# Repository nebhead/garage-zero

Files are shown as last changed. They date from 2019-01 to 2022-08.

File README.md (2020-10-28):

# Garage-Zero

## Raspberry Pi Zero based Garage Door Control & Status

***Note:*** *This project is continuously evolving, and thus this readme will likely be improved over time, as I find the inspiration to make adjustments.  That being said, I'm sure there will be many errors that I have overlooked or sections that I haven't updated.*

This project was inspired by Chris Driscoll's "Idiot's Guide to a Raspberry Pi Garage Door Opener" (http://www.driscocity.com/idiots-guide-to-a-raspberry-pi-garage-door-opener/).  I've replicated Chris' hardware setup almost exactly, save for the Raspberry Pi Zero (instead of the Raspberry Pi Model B).  

Instead of using the WebIO libraries that Chris uses, I decided to implement things a bit differently, providing a dynamic webUI with bootstrap and Flask.  

Initially this project used Flask's native WSGI services without Gunicorn or nginx as a proxy.  However, I noticed that after some time, the app would become unresponsive.  After a little research, it appears that Flask's built in web server is for testing purposes only and shouldn't really be used in production.  With that said, I'm using Gunicorn and nginx to proxy web requests.  This is simple enough to configure and setup, however I had to redesign the application without the threading libraries, due to conflicts with Gunicorn.  Instead, I am using two processes running concurrently (control.py and app.py).  Control handles all of the RasPi GPIO interfaces, while App handles the web routes.  They communicate through a .json file that is human readable for simplicity.  

## Screenshots

The interface / webui is broken out into three main pages. The first is the dashboard view where you can check the current status of the garage door (whether it is open or closed), see the event history (button presses, opened/closed, notifications, reboots, etc.), and of course a large button to open/close the door (which also indicates green if closed, red if open).

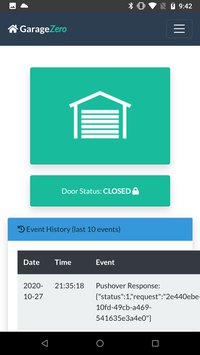
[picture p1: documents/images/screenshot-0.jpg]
Dashboard


Pressing the hamburger icon in the upper right of the interface, allows you to go to the history page, which gives you the detailed history of the last month of events.  

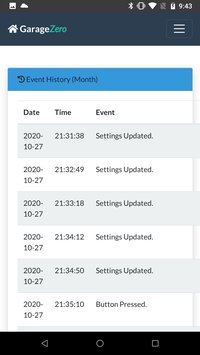
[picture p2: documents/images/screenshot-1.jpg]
History


Pressing the hamburger icon in the upper right of the interface, allows you to also access to the administration screen. This interface allows you to configure the notification settings (i.e. e-mail, IFTTT notifications, and Pushover notifications).

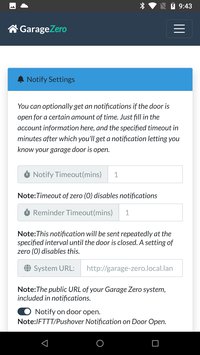
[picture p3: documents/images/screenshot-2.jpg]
Admin & Settings


Scrolling down gives you the ability to select from a few different themes including a 'dark mode' for those times when you don't want to blind yourself at night.  Then more system information following the theme settings.  

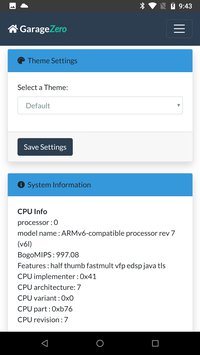
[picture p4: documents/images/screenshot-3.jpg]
Admin 2


Scrolling down further gives you the option to reboot the system or shutdown the system.  

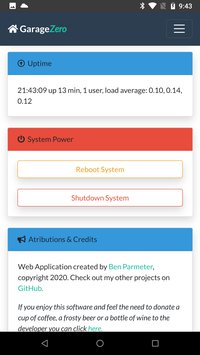
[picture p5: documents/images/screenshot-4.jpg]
Admin 3


## Hardware Configuration

### The Parts List
The parts list and setup of this was heavily borrowed from the following guide here: [http://www.driscocity.com/idiots-guide-to-a-raspberry-pi-garage-door-opener/](http://www.driscocity.com/idiots-guide-to-a-raspberry-pi-garage-door-opener/)

* **Raspberry Pi Zero W** - Technically any Raspberry Pi with wireless capability will do fine, but for this application a Raspberry Pi Zero W works really well.  
* **Case for Raspberry Pi** *(optional)* - It's a good idea to have a case for the Pi and other electronics to shield it from environmental abuse.  I personally decided to develop a 3D printed case and have shared the STL files for you if you want to duplicate my setup. [Link to case files.](documents/case) For reference, I used an Creality Ender 3 to print the case, with 0.12 layer height.  I'm reasonably happy with the finished product, but your mileage may vary.  
* **2-Channel Relay** - I use both channels for one single door to prevent any spurious door open signals from being sent during reboot/shutdowns. [Amazon Link](https://www.amazon.com/dp/B0057OC6D8/ref=cm_sw_em_r_mt_dp_U_jtppCb3FQ787B)
* **Magnetic Switch** (This is only necessary if you want to be able to determine if the door is open or closed) [Amazon Link](https://www.amazon.com/dp/B0009SUF08/ref=cm_sw_em_r_mt_dp_U_htppCbJ7B52KG)
* **Wire** for the magnetic switch and connecting the Raspberry Pi to your garage door opener (I used extra CAT6 cable I had laying around, any 2-conductor cable ~20-24 gauge should be fine)
* **Micro SD Card** - Greater than 4GB is probably good.  
* **MicroUSB Power Adapter** - At least 1 amp current recommended.  Make sure you have a place to plug this in near your garage door opener
* **10k Ohm resistor** - Used for the resistor divider circuit on the magnetic switch. Prevents the switch input from floating and causing spurious inputs.
* **1k Ohm resistor** - Used for the resistor divider circuit on the magnetic switch. Prevents the switch input from floating and causing spurious inputs.

### The Schematic

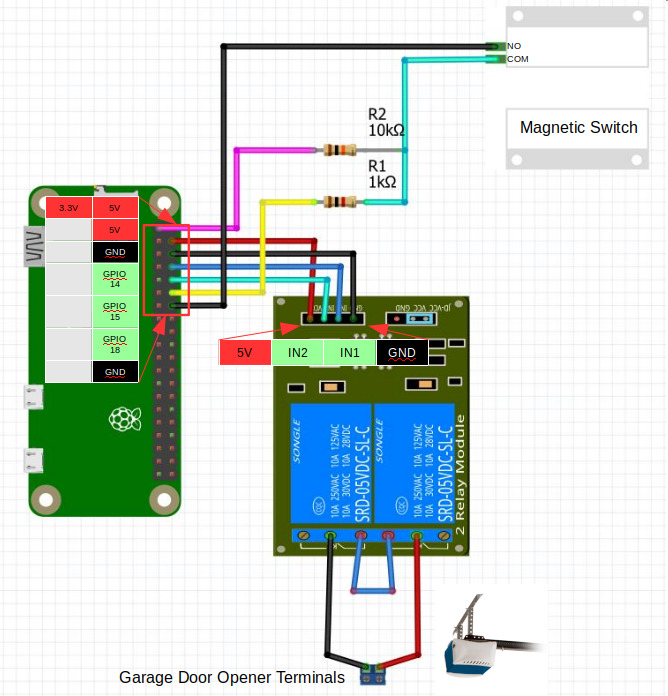
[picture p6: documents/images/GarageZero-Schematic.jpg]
Schematic


#### GPIO Mapping
The following GPIOs are mapped for this project:
* **GPIO15** - Output Relay Control (Open / Close Garage Door)
* **GPIO14** - Output Relay Control Gate (Prevents spurious open/close events during power-on, shutdown and reboot cycles) **IMPORTANT:** This relay should have a wire connected to the Normally Closed (NC) side of the relay. Otherwise, it will not function properly, preventing all button presses.
* **GPIO18** - Input for Magnetic Switch (Current State of Garage Door)

**Note:**  *Optional design change.*  Per user [hmoffatt](https://github.com/hmoffatt), there may not be a need for the 1k pull-down resistor.  It is probably OK to have the switch ground the input. Secondly there are fixed pull-up resistors of 1.8k on GPIOs 2 and 3 of the Raspberry PI. So you can just connect the switch directly to +3.3V and GPIO 2 or 3 without adding any extra resistors. If you make this design change, make sure you change the GPIO definition in the code from GPIO18 to GPIO2.  

**Note:** If you want to change which GPIOs you would like to use, please modify the control.py constants to what you want to use. Edit the following lines(*in control.py*):

```
    # GPIO Definitions
    relay_pin = 15			# GPIO 15, Pin 10 (RasPi Header)
    relay_gate_pin = 14		# GPIO 14, Pin 08 (RasPi Header)
    switch_pin = 18			# GPIO 18, Pin 12 (RasPi Header)
```

Truth Table for visualizing the output:

| IN1 | IN2 | Relay1 | Relay2 | Button Output |
|:---:|:---:|:---:|:---:|:---:|
|  0  |  0  | C | O | Not Pressed |
|  0  |  1  | C | C | Pressed |
|  1  |  0  | O | O | Not Pressed |
|  1  |  1  | O | C | Not Pressed |

*C=Closed/Connected*

*O=Open/Not Connected*

### Photos of the Hardware

A picture is worth a 1000 words.  With that, here is a bunch of pictures (with some words).  

Here is a picture of the Raspberry Pi Zero and the 2-channel relay module in the 3D-printed case.  Note that only the pins being used for GPIOs, GND, & Power on the header have been populated.  
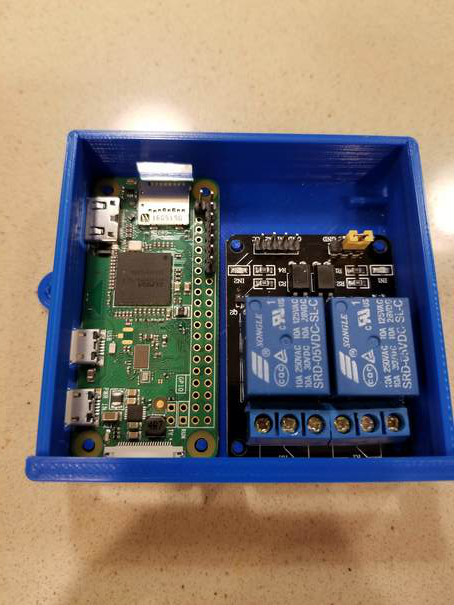
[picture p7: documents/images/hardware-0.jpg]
Case and Boards


I built this little daughter board to interface the Raspberry Pi with the 2-Channel relay board, as well as break-out wires for the magnetic switch/sensor.  The nice thing about this board is that it has headers that plug directly into the boards very easily (pictured here).
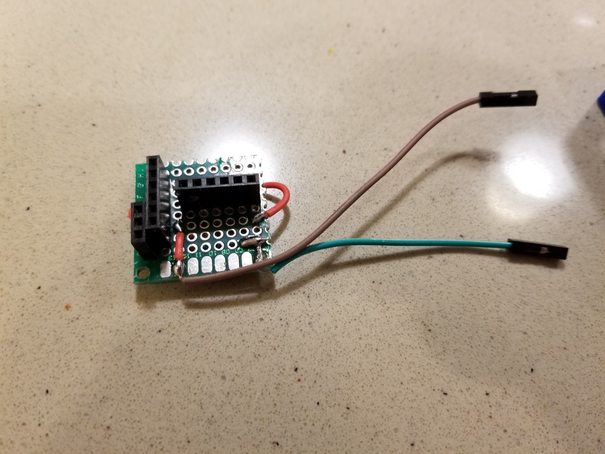
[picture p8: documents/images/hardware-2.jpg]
Daughter Board (Bottom)


This is picture of the top of the daughter board (and the case/rpi/relay), which has the wire routing, and the two resistors (for the voltage divider).  
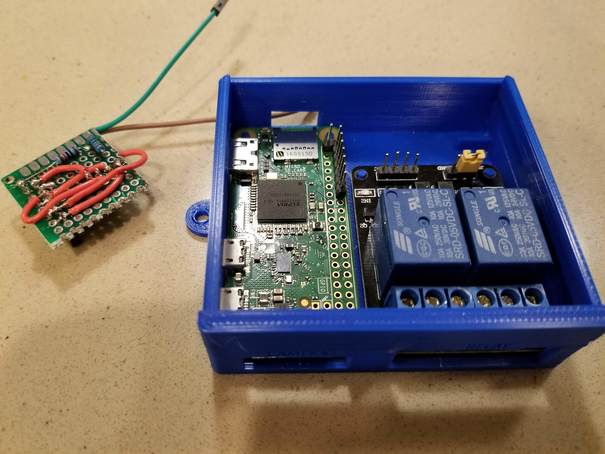
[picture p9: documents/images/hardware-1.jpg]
Daughter Board (Top), Case, RPi, Relay


Picture of the daughter board actually plugged into the raspberry pi and relay inside the case.  This gives you a picture of the scale.  
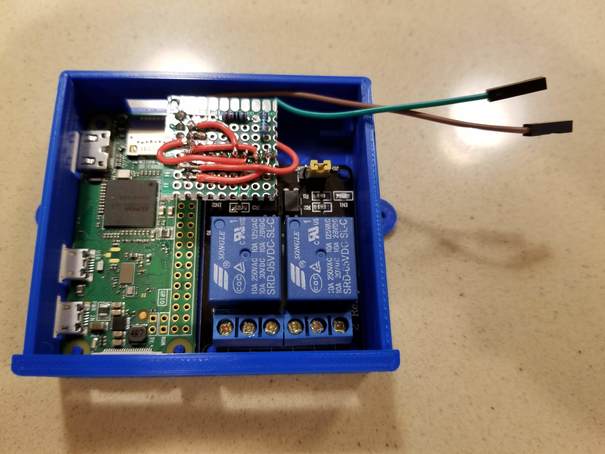
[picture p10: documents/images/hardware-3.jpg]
Daughter Board (Top) installed, Case, RPi, Relay


This is an attempt at showing the daughter board installed in both the raspberry pi and the relay.   
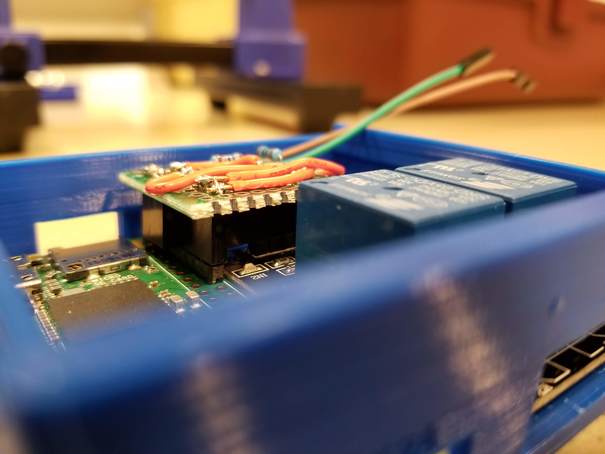
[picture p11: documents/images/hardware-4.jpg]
Daughter Board installed, side view


The female pin connectors are hot-glued into the space in the corner of the case so that the magnetic sensor can be easily connected via male jumper pins.  Note that the rest of the boards have been hot-glued into place.  
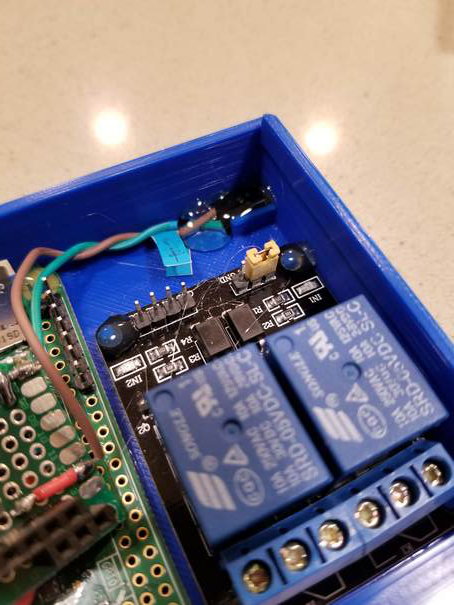
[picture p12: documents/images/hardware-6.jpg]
Hot Glue for the win


The assembled kit all together in the case, with lid.  Note that the screws are still accessible from the top.  
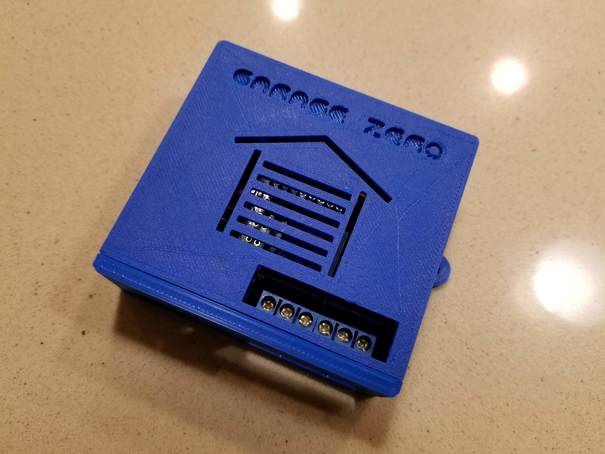
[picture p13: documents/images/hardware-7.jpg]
Case assembled


Case mounted to the beam directly above the garage door opener using two screws on either side of the case.  
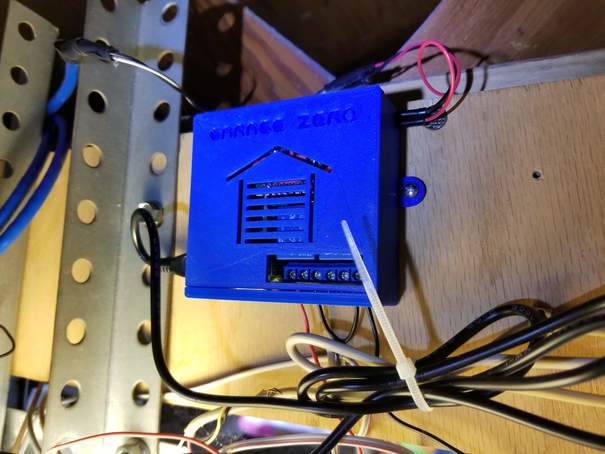
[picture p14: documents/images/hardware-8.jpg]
Installed above garage door opener


Another view of the installed case, with power cord. plugged in.
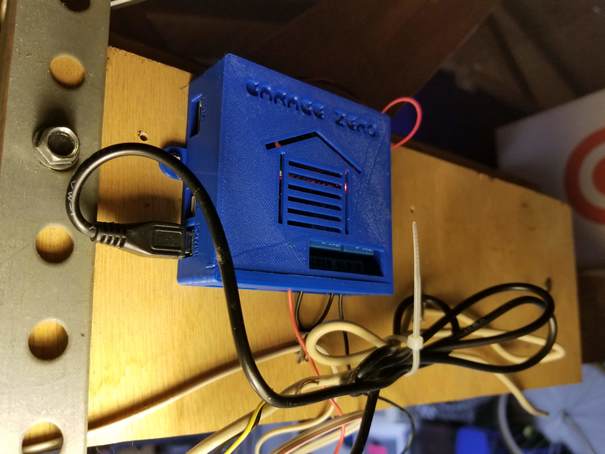
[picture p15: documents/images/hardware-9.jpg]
Installed view 2


Another view of the installed case, with the garage door opener for scale.
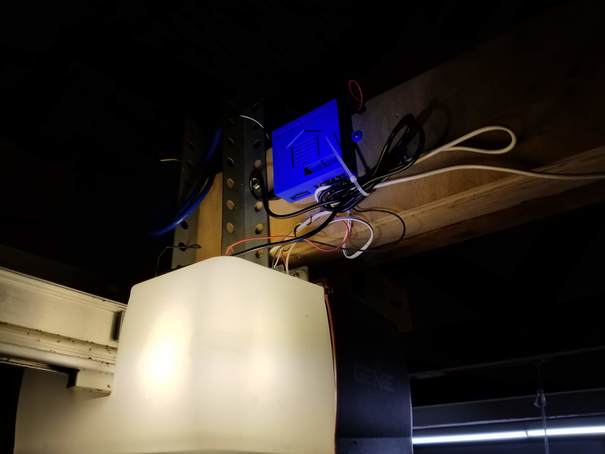
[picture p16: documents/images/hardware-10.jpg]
Installed view 3 zoomed out


Connections to the garage door opener terminals from the relay in the case.
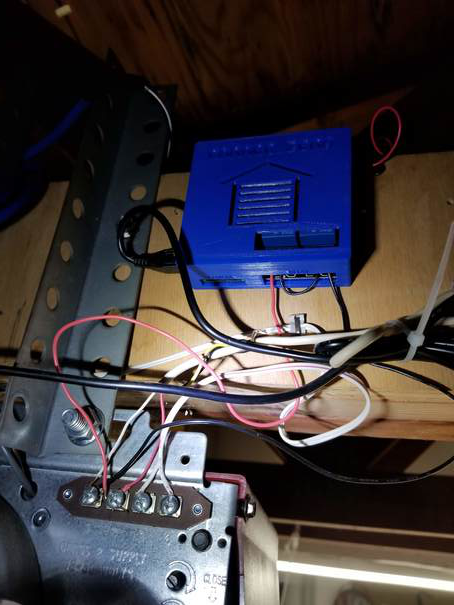
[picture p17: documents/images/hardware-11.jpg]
Garage Door Opener Terminal Connections


View of the magnetic switch, mounted to the top of the garage door.  The wires connected via the CAT6 cable.  
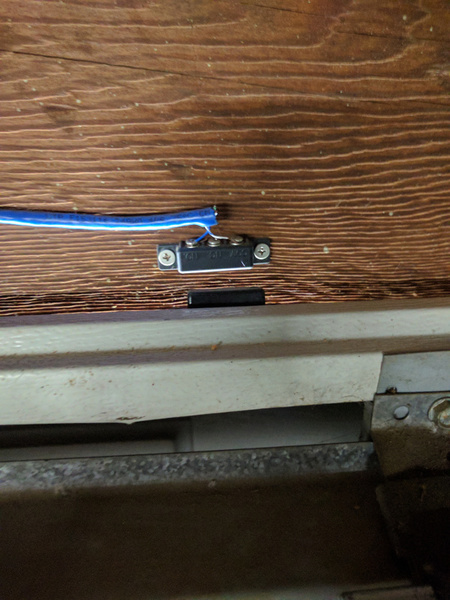
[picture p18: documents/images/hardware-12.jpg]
Magnetic Switch


## Software Installation:

### Walkthrough Installation Video (for old version)

Added a walkthrough of the installation instructions on [youtube](https://youtu.be/OK_EWe1pKeE).  You'll probably still want to refer to the below instructions, but it's nice as a reference to see the install process in action.  

### Raspberry Pi Zero Setup Headless (*from raspberrypi.org*)
Once you've burned/etched the Raspbian Stretch Lite image onto the microSD card, connect the card to your working PC and you'll see the card being mounted as "boot". Inside this "boot" directory, you need to make 2 new files. You can create the files using Atom code editor.

+ Step 1: Create an empty file. You can use Notepad on Windows or TextEdit to do so by creating a new file. Just name the file **ssh**. Save that empty file and dump it into boot partition (microSD).

+ Step 2: Create another file name wpa_supplicant.conf . This time you need to write a few lines of text for this file. For this file, you need to use the FULL VERSION of wpa_supplicant.conf. Meaning you must have the 3 lines of data namely country, ctrl_interface and update_config

```
country=US
ctrl_interface=DIR=/var/run/wpa_supplicant GROUP=netdev
update_config=1

network={
    ssid="your_real_wifi_ssid"
    scan_ssid=1
    psk="your_real_password"
    key_mgmt=WPA-PSK
}
```

#### Run RasPi-Config
```
ssh pi@192.168.1.xxx

sudo raspi-config
```
+ Set locales
+ Set timezone
+ Replace Hostname with a unique hostname ('i.e. garage-zero')

### Automatic Software Installation (Recommended)

I've created a script to install this automatically and I believe it will work well with at least Raspberry Pi OS Buster (08-2020).  Your mileage may vary, and if you experience any trouble try the below Manual Install.

After you've done the above steps to configure your raspberry pi, at the command line type the following:

```
curl https://raw.githubusercontent.com/nebhead/garage-zero/master/auto-install/install.sh | bash
```

Follow the onscreen prompts to complete the installation.  At the end of the script it will reboot, so just be aware of this.  

### Manual Software installation (If the Auto Install Fails)

#### Make the /tmp directory in RAM based storage
```
echo "tmpfs /tmp  tmpfs defaults,noatime 0 0" | sudo tee -a /etc/fstab > /dev/null
```

#### Give pi user access to the GPIO pins
```
sudo adduser pi gpio
```

#### Install Git, Python PIP, Flask, Gunicorn, nginx, and supervisord
```
sudo apt update
sudo apt upgrade
sudo apt install python3-dev python3-pip python3-rpi.gpio nginx git gunicorn3 supervisor -y
sudo pip3 install flask
git clone https://github.com/nebhead/garage-zero
```

### Setup nginx to proxy to gunicorn

```
# Move into garage-zero install directory
cd ~/garage-zero

# Delete default configuration
sudo rm /etc/nginx/sites-enabled/default

# Copy configuration file to nginx
sudo cp garage-zero.nginx /etc/nginx/sites-available/garage-zero

# Create link in sites-enabled
sudo ln -s /etc/nginx/sites-available/garage-zero /etc/nginx/sites-enabled

# Restart nginx
sudo service nginx restart
```

### Setup Supervisor to Start GarageZero on Boot / Restart on Failures

```
# Move into garage-zero install directory
cd ~/garage-zero/supervisor

# Copy configuration files (control.conf, webapp.conf) to supervisor config directory
# NOTE: These files all assume you are using the Pi user and standard install directory.  If you used a different directory for garage-zero then make sure you edit the *.conf files appropriately
sudo cp *.conf /etc/supervisor/conf.d/

# If supervisor isn't already running, startup Supervisor
sudo service supervisor start

# If supervisor is running already, just reload the config files
sudo supervisorctl reread
sudo supervisorctl update

# Or just reboot and supervisord should kick everything off
sudo reboot
```
Optionally, you can use supervisor's built in HTTP server to monitor the scripts.

Inside of /etc/supervisor/supervisord.conf, add this:

```
[inet_http_server]
port = 9001
username = user
password = pass
```
If we access our server in a web browser at port 9001, we'll see the web interface that shows the status of the two scripts (WebApp and Control).  This gives you a quick and easy way to monitor whether any of the scripts has stopped functioning.  

### Configure Crontab for Log Backups

Configure crontab for the first time, to enable log backups on a monthly basis.

Edit crontab by starting crontab in edit mode.
```
sudo crontab -e
```

The first time this is run, it will ask you what editor you want to use.  I personally like to use nano, so I select this option.  

Add the following line to the end of the file:
```
0 0 1 * * cd /home/pi/garage-zero/logs && sh backup.sh
```
Then press CTRL-O to write out to the file the CTRL-X to exit the program.  

### Note on Addons

We've had one user submitted add-on which includes both camera integration and LED lighting.  I've added an addon folder for the necessary files and documentation to supoport addons.  If we have any additional features that are user submitted (and not part of the base install) this is the right place to include them.  

## Using GarageZero
If you've configured the supervisord correctly, GarageZero scripts should run upon a reboot.  Once the system is up and running, you should be able to access the WebUI via a browser on your smart phone, tablet or PC device.  

Simply navigate to the IP address of your device for example (you can usually find the IP address of your device from looking at your router's configuration/status pages). My router typically assigns IPs with prefixes of 192.168.1.XXX.  I'll use examples on my home network here, so you'll see URLs like: http://192.168.1.42  Yours may look different depending on your routers firmware/manufacturer (i.e. 10.10.0.XXX, etc.)

**Note:** It's highly recommended to set a static IP for your Pi in your router's configuration.  This will vary from manufacturer to manufacturer and is not covered in this guide.  A static IP ensures that you will be able to access your device reliably, without having to check your router for a new IP every so often.   

The interface / webui is broken out into three main pages. The first is the dashboard view where you can check the current status of the garage door (whether it is open or closed), see the event history (button presses, opened/closed, notifications, reboots, etc.), and of course a large button to open/close the door (which also indicates green if closed, red if open).

Dashboard

Pressing the hamburger icon in the upper right of the interface, allows you to go to the history page, which gives you the detailed history of the last month of events.  

History

Pressing the hamburger icon in the upper right of the interface, allows you to also access to the administration screen. This interface allows you to configure the notification settings (i.e. e-mail and/or IFTTT notifications).

Admin & Settings

Scrolling down gives you more information about the system hardware, and the uptime.  

Admin 2

Scrolling down further gives you the option to reboot the system or shutdown the system.  

Admin 3

### Adding GarageZero to your Homescreen using Chrome on your Android Phone

If you are an Android person, you are likely to be using Chrome on your phone and can not only setup a link to the web-app on your homescreen, but it also makes the interface look like a native application.  Pretty cool right?  Well here's how you set this up, it's very simple.  

First, navigate to the instance of GarageZero in your Chrome browser on your phone.  Remember, it's as easy as going to the IP address that was assigned to you device.  Then, from the Chrome drop-down menu in the upper right of the screen, select "Add to Home screen".  

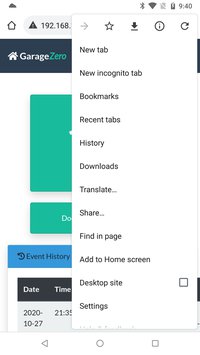
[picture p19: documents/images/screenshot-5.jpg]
Add to Home screen in Chrome


Then, when the new dialog box pops up, you will have the opportunity to rename the application, or keep the default.

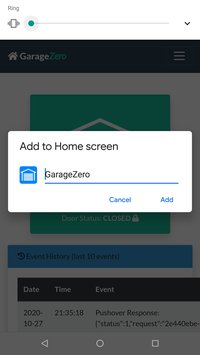
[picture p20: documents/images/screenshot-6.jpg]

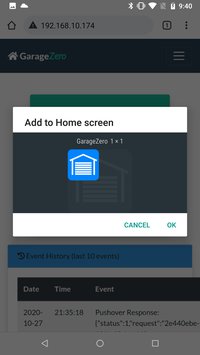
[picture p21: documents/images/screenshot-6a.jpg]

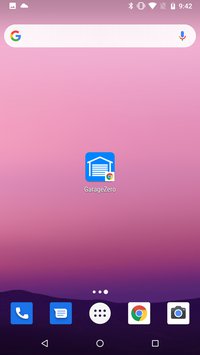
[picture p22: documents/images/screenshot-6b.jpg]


And there you have it, you've not only created a quick link to your garage door web-app, but you've also created a pseudo application at the same time.

### Set up e-mail notifications

Navigate to your administration and settings page in the web app.  From here, you can configure your notification settings.  Simply enter your e-mail credentials for the account you want to send FROM in the FROM E-mail box.  Then enter the e-mail address for the account you want to send e-mail notifications to in the TO E-mail box.  Then enter the SMTP server for the FROM E-mail account, the SMTP port and your password.  (UPDATE April 2019: It's now possible to enter multiple e-mails in the TO e-mail field, separated by commas)

Finally, set the time in minutes that the garage door is open before sending a notification and click on "Save"

That's it!  

Admin & Settings

### Set IFTTT notifications
If you are familiar with IFTTT then you can use this to setup an app notification on your smart phone.

Use the [Maker WebHooks applet](https://ifttt.com/maker_webhooks) to setup [notifications](https://ifttt.com/if_notifications).  

GarageZero uses the following event types:
* GarageEvent_Open_Alarm
	* 'value1': minutes
* GarageEvent_Closed
* GarageEvent_Notify_on_Open

For each of the event types above, simply create a WebHook applet that triggers on those events and sends a notification via the application.  

Example of WebHook for GarageEvent_Open_Alarm:

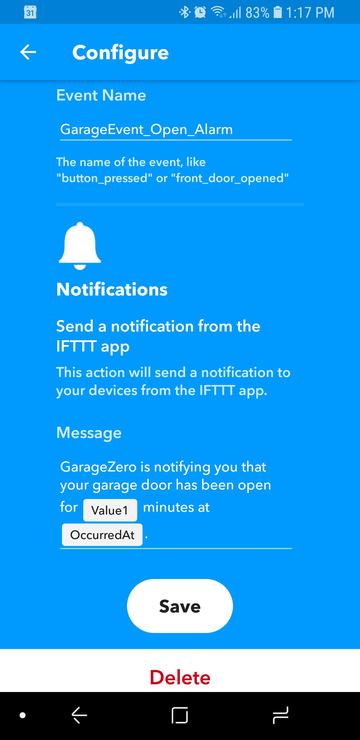
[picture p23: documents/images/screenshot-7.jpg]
IFTT App GarageEvent_Open_Alarm


Example of WebHook for GarageEvent_Closed:

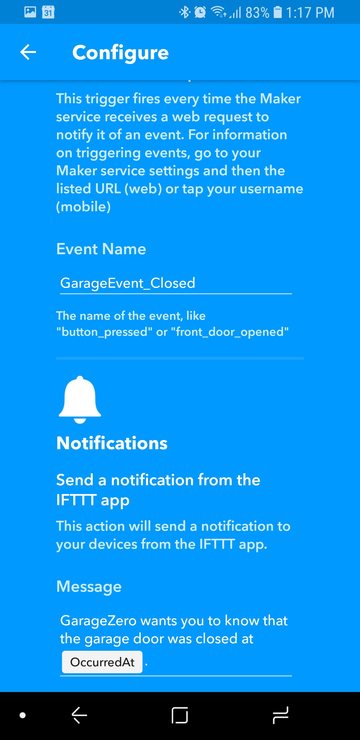
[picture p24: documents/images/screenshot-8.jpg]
IFTT App GarageEvent_Closed


All that is needed to be configured on the web-app is to populate your IFTTT API Key in the administration/settings page under notification settings.  

Make sure you also configure the notify timeout (mins) or notifications will be disabled.  Once you've done this click save to apply the settings.

**Note:** You can also set IFTTT to notify you when the door is opened (no delay), by selecting the option to notify on open.  This currently only works for IFTTT notifications, not e-mail notifications.   

Admin & Settings

### Accessing GarageZero from outside your local network

Please take the utmost care in considering options for exposing GarageZero outside of your home network. Given that GarageZero has no real security built-in, anyone that is able to gain access to it directly or indirectly, may be able to control your garage door hardware which could result in damage to your property or even potentially physical harm to someone nearby.  

If you want to have access to GarageZero outside of your home network, and I haven't already convinced you not to do this, then I would recommend setting up a VPN for your local network.  This would allow you to tunnel to your home network and access all of your local equipment with some level of security.  A good, low cost, and dead simple VPN project I would recommend is [PiVPN](http://www.pivpn.io/).

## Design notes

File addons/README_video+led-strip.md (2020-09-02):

VIDEO SETUP

Open index.html and add camera ip address.

sudo nano garage-zero/templates/index.html

1. Uncomment (remove <!-- and --> from beginning and end) of the following line.

<!--<center><img name="main" id="main" border="0" width="400" height="300" src="http://[camera ip]:[port]/video"></center> -->

2. Enter the cameras ip and port number.

GARAGE LED STRIP LIGHTS

1.COPY TO garage-zero folder.

garage-led-strip.py
garage-led-strip.service
garage-led-strip.sh

2.Copy the garage-led-strip.sh to /usr/bin and make it executable:

sudo cp garage-led-strip.sh /usr/bin/garage-led-strip.sh
sudo chmod +x /usr/bin/garage-led-strip.sh

3.Copy garage-led-strip.service to /etc/systemd/system and give it permissions:

sudo cp garage-led-strip.service /etc/systemd/system/garage-led-strip.service
sudo chmod 644 /etc/systemd/system/garage-led-strip.service

4. Test

sudo systemctl start garage-led-strip.service   # May get a warning to reload daemon

5. Check status

sudo systemctl status garage-led-strip.service

6. Stop and restart service

sudo systemctl stop garage-led-strip.service
sudo systemctl restart garage-led-strip.service

7. Enable the service 

sudo systemctl enable garage-led-strip.service

8. Reboot the linode manager

sudo systemctl status garage-led-strip.service

9. Test on reboot of pi.

10. Adjust time.sleep in garage-led-strip.py

sudo nano garage-zero/garage-led-strip.py

This adjustment makes allowance for a dimming light source (original garage opener lights) that the photdiode is detecting. A dimming light source can trigger the GPIO pin to read high/low/high repeatly which will switch the relay on and off until the light source eventually goes out.

-if your light source does not dim before going out, time.sleep at the end of the script can be set between 0.2 and 2.5. [e.g time.sleep(0.2)]
-if you light source gradually dims, play around with the sleep time to prevent the relay triggering as light source dims. [default is time.sleep(2.5)]

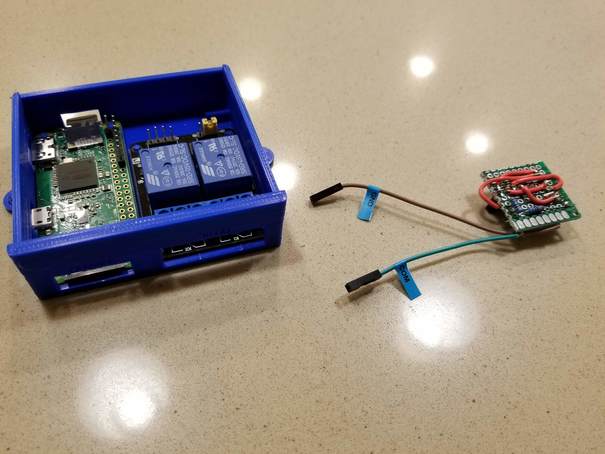
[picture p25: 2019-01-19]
documents/images/hardware-5.jpg

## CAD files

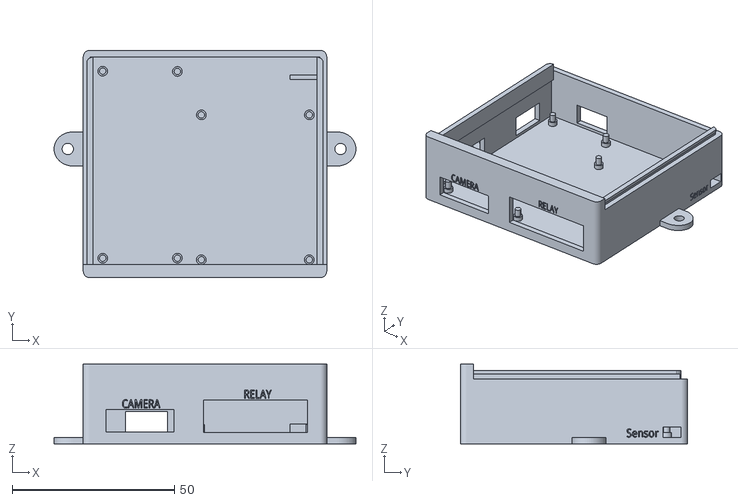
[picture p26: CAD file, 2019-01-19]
documents/case/Garage Zero Case.stl
93.0 x 70.0 x 24.5

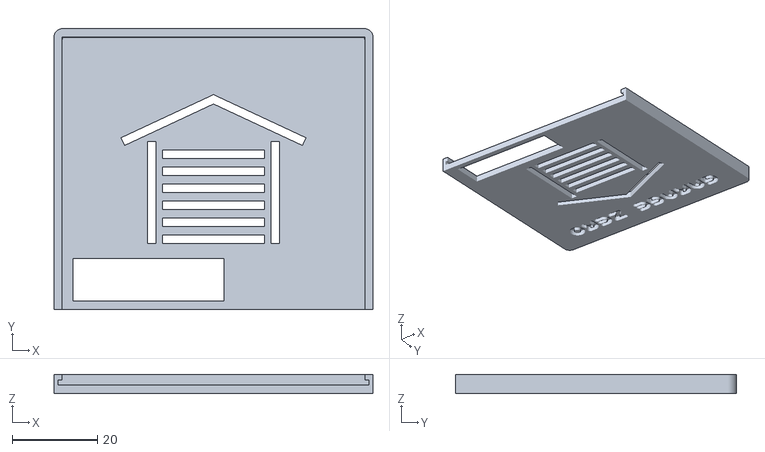
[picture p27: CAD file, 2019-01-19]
documents/case/Garage Zero Lid.stl
75.0 x 66.0 x 4.50

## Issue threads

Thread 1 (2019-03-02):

gunicorn proxy bad gateway 502 redirect?

ArashTajalli, 2019-03-02:
Hey there this is my first git anything to keep in mind a bit of noobiness that may come along the way but, I'm trying to figure out the problem with what I think is Gunicorn not being setup correctly to proxy for NGINX. I've followed the directions to the Tee, I even flashed my SD card with a blank slate. But I keep getting stuck at a 502 Bad Gateway and I've confirmed that my routers and firewalls aren't blocking the ports. The config files are all working fine and services are also healthy and running and ps aux shows them working.

> 2019/03/02 15:20:57 [error] 13533#13533: *1 connect() failed (111: Connection refused) while connecting to upstream, client: IP-hidden, server: , request: "GET / HTTP/1.1", upstream: "http://127.0.0.1:8000/", host: "IP-hidden"

certain IP addresses hidden for my ofwn protection

Part of it is working with me being able to access the client IP:9001 and getting those 2 controls. So I know the project isn't at a total loss for me.

BTW The project altogether looks great! it's been a real joy getting comprehensive instructions and the hardware stuff :D

2 hours later?:
the /etc/nginx/{sites-enabled, sites-available}/garage-zero files were missing a "garage zero" right next to "location /"

So
```
server {
    location ~/garage-zero {
        ...
    }
}

```

However now I'm greeted with a "welcome to nginx!" which is a sight for sore eyes after so much config scouring.

nebhead, 2019-03-02:
Very strange... when you try your pi's IP at port 5000, what do you see?

nebhead, 2019-03-02:
Also, your sites-enabled/available file should look more like this:

`server {
    location / {
		proxy_pass http://127.0.0.1:8000;
		proxy_set_header Host $host;
		proxy_set_header X-Real-IP $remote_addr;
	}
`

nebhead, 2019-03-02:
Also, try port 8000.  So, try:

your.pi.ip.address:5000
your.pi.ip.address:8000

If either of those is working then your Flask app.py is running ok, but perhaps we need to go back to nginx and see what's going on there.

ArashTajalli, 2019-03-03:
In your second comment that compares mine I was shorthanding it due to rebooting the pi, the only difference really was:

>location / {
#gives me the 502 bad gateway
>location ~/garage-zero {
#gives me the "welcome to Nginx" page

Entering the 5000 and 8000 ports I've gotten nothing in the web browser: Firefox prompt "unable to connect" Which surprises me that it doesn't work because I made sure pip did install flask with sudo.

I am considering making an image of this SD card back it up on my HDD and reflash it again with a fresh lite install so I can start from zero once more. (Hell I'll make a private youtube video so I don't look insane) Thanks for keeping up with this thread

Originally I thought there were some public IPs in here but it looks like I'll be fine sharing logs about devices within my local network.

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

nebhead, 2019-03-03:
Oh it's no problem, I am just really happy someone is using my little project. :)

So, since this appears to be an nginx proxy type issue, maybe let's try to nuke nginx and re-install.

`sudo apt purge nginx nginx-common # Removes everything`

At this point you might test accessing the gunicorn/flask application directly again by going to 10.0.0.22:8000.  But honestly, you can probably go straight to reinstalling nginx.

`sudo apt install nginx -y`

Then do the nginx config again:

```
# Make sure you're in the right directory
cd ~/garage-zero

# Delete default configuration
sudo rm /etc/nginx/sites-enabled/default

# Copy configuration file to nginx
sudo cp garage-zero.nginx /etc/nginx/sites-available/garage-zero

# Create link in sites-enabled
sudo ln -s /etc/nginx/sites-available/garage-zero /etc/nginx/sites-enabled

# Restart nginx
sudo service nginx restart
```

After all this, give it another try (or reboot first and try again).

I'm going to walk through the install process again on a pi that I have laying around myself to confirm.  It's possible that something has changed in a newer version of raspbian, or nginx that is goofing things up.  And I really like your idea of making a video - that might be something I add to this project as a walkthrough / tutorial.

nebhead, 2019-03-04:
Well, after running through my own instructions, it seems I have exactly the same error.  My issue appears to be one with Flask and Gunicorn though.  I will need to debug a bit more, but thanks for pointing this out.  I'll post an update when I have a chance to get to the bottom of this.

ArashTajalli, 2019-03-04:
Much appreciated! I'm certain its the same issue between us. I didn't bring my pi with me to test it out during my travels, but if I happen to dig around and successfully solve it myself I'll branch the project. And I'm glad you put it up! We all learn in this process of testing and deploying and I've come to learn a lot more about these newer tools.

I've put off the same project for so long and finally got the time to see if others like you have made a modern-ish solution compared to my lamp stack solution that I can't remember what I did. anyways cheers I hope the solution comes to you sooner than later. o/

nebhead, 2019-03-04:
Figured it out!

Somehow, I had inserted an error into my webapp.conf file for supervisord.  Basically, the way that I was launching gunicorn (using an explicit path to the app in the command) was causing gunicorn to crash.  Supervisor was trying to restart the app over and over, but to no avail.  Anyway, nginx will throw up a bad gateway when there is nothing handling the requests - and in this case since gunicorn was crashing it wasn't responding.

So the fix is to change the following line in the webapp.conf file in /etc/supervisor/conf.d/ directory from:
`command=/usr/bin/gunicorn /home/pi/garage-zero/app:app`
to:
`command=/usr/bin/gunicorn app:app`
And after a reboot, you should be golden.

I'm working on updating the git repo with this change, as well as a few modifications to the documentation that I found along the way.  I did want to sincerely thank you for bringing this to my attention.  I wouldn't have found this or fixed it without you calling it out.  Give this a try and let me know how it goes.  I'll close this issue once you've confirmed it.  Thanks again!

ArashTajalli, 2019-03-05:
Guh Sweet release, you've certainly done a great job and have helped me and others who stumbled onto this project, cheers man!

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

nebhead, 2019-03-05:
You are welcome!  Thanks for making it better, and thanks for giving it a try!

Closed 2019-03-05.

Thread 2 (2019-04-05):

Write state.json to temporary storage

hmoffatt, 2019-04-05:
Can I suggest writing states.json to temporary storage, instead of to the current directory which will usually be on the SD card? There's no need to write that to SD card every time and wear out the card.

/run is on tmpfs (in-RAM storage), although the pi user won't have write access to it by default so that would need to be set up on boot for the states file. The pi user can write to /run/user/1001, but root won't know where to find that.

nebhead, 2019-04-05:
First of all, I wanted to thank you for giving so much valuable feedback on this project.  It is humbling to me that anyone one take the time to dive in a help make my little project better.  So a big hearty thank you!

OK, so, this is a really, really cool idea.  I have been concerned to some degree with flash wear-out, but wasn't sure how to tackle this.  I feel like this is a great option, but I also will need to do some research on this to understand the limitations and how I can use this.  Give me some time, but I will definitely look into implementing this one.

Thanks!

hmoffatt, 2019-05-23:
Thinking about this some more, I think you could just run the control and web interfaces in one program and avoid writing the state to the file system at all.

If the pi user is added to the gpio group, they can access the GPIOs (no need to be root, as long as you're not trying to run it on port 80). This is a good idea anyway rather than running it as root.

Then if you ran the control loop as a separate thread from the wsgi app, they can just share the state in memory and never write it to the file system.

nebhead, 2019-05-23:
Definitely a good idea, and what I wanted to do from the beginning.  However, I just couldn't get threading to work with Gunicorn. Was starting to look at Gevent to see if there was a "proper" way to have a background thread while using Gunicorn. Still haven't gotten that to work. Seems like Gevent threads are blocking. Any help here would be greatly appreciated.

hmoffatt, 2019-05-24:
Alternatively you could actually create the control thread and also the gunicorn application directly from python, rather than expecting the web app to be launched from gunicorn at the command line. What I mean is: http://docs.gunicorn.org/en/stable/custom.html. Then the thread is completely separate to the gunicorn instance?

hmoffatt, 2019-05-24:
It seemed to work OK when I started the control loop on a thread before the Flask app was created, but if gunicorn was ever set up for >1 worker than it would create the app (and the background thread) for each worker, which wouldn't be good.

So I used the custom gunicorn app approach and this is working. It starts the control thread, then starts gunicorn. I haven't removed the reading/writing of the state/config to file all the time yet though so it's not ready to merge. It's pretty simple though: https://github.com/hmoffatt/garage-zero/commit/c1a428e6132dbe286b76febf4ef8453dd2b034b5

nebhead, 2019-05-26:
Excellent!  This is super interesting to me because it would simplify a couple of other projects that I have currently as well.  As soon as you get it all merged, let me know.  I'm eager to check it out so I can update this project and others!

nebhead, 2019-10-11:
Thanks to user @ruddj we can close this one.

Closed 2019-10-11.

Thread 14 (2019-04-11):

Pins swapped

hmoffatt, 2019-04-11:
I noticed when I wired up the hardware that I had to swap the two relay GPIOs to get it working.

I think there is a small bug:
Relay IN1 is used as the relay gate pin, you set it to 0 and don't change it in the code.
Relay IN2 is the relay control pin, you toggle this to press the button.

In the diagram IN1 = GPIO 14, IN2 = GPIO 15.

But in the code they are declared the other way around - relay_pin = 14, relay_gate_pin = 15.

nebhead, 2019-04-11:
Gah!  Thanks for catching this.  I actually have had this comment before which was why I had added the truth table in the readme file - to prove to myself that it was setup correctly.  But I assumed I had documented the picture to the code correctly.  I guess I goofed!

I'll make the swap in the code so that I don't have to modify the picture at all.  Thanks again!

Closed 2019-04-11.

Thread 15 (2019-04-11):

Change to sensor input

hmoffatt, 2019-04-11:
This is more of a note for anyone else wanting to set up a Garage-Zero and might be better in a wiki article than an issue, so feel free to just close it!

I think the door sensor input is more complicated than it needs to be. This is the same for the hardware design you started with (http://www.driscocity.com/idiots-guide-to-a-raspberry-pi-garage-door-opener/), and the one HE started with (http://freemansgarage.com/blog/?p=587).

The design has a 10k pullup resistor and a 1k pull down. Firstly there is no need for the pull down, it is ok to have the switch ground the input. Secondly there are fixed pullup resistors of 1.8k on GPIOs 2 and 3 of the Raspberry PI. So you can just connect the switch directly to +3.3V and GPIO 2 without adding any extra resistors.

One of the commenters on the original article suggested this, and the author said it didn't work for him. It's working fine for me though.

nebhead, 2019-04-11:
Well that's good news!  Frankly, I just blindly followed the original articles advice, as when I started this project I was pretty new to the whole thing.  But absolutely true I think that the pull-down is probably not necessary.  I can add a note to the readme as such.

hmoffatt, 2019-04-11:
I was going to go find the resistors and solder something up, but then I got lazy and started studying the circuit instead!

The 1.8k pullup on GPIOs 2 and 3 is stronger than the 10k external so I can't think why the original designer would have had any problem with that.

Closed 2019-05-24.

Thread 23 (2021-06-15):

Magnetic Switch to confirm Open door

J0eK1ng, 2021-06-15:
Hi,

My original wireless garage door opener failed a few weeks ago and I have been upgrading several RPi 3 to RPi4. I would like to use your Garage door opener with one of my now unused RPi3.
I realize this is not an issue but more a feature request. Would it be possible to add a Magnetic Switch at the doors fully open position and also have your code report this in your interface? This would confirm that the door is actually open and not potentially partly open or closed. I know its probably overkill but it is a security concern for me not really knowing the actual status of the door unless its closed.

Thanks

Denis

nebhead, 2021-06-15:
Hey Denis - Yeah, I've actually thought about this as well.  Definitely could be something that could be added as an optional feature. Actually, I wonder if there is a good way to tie into the existing microswitch for the shut-off.  Maybe that's overcomplicating things though.  I'm currently away from my workshop for a while - so it may be some time before I'm able to implement the update, but I'll likely get around to it then.  I wouldn't mind having this feature too.

J0eK1ng, 2021-07-04:
I'm also thinking that it would be convenient to be able to turn on/off the light on the garage door motor with a relay. That would be a plus for me. What do you think?
Denis

J0eK1ng, 2021-07-27:
I have been using GarageZero for 2 weeks now and really love it. I have also changed the door status pic to these animated png files of Peter Griffin I like them :)
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

J0eK1ng, 2021-07-27:
Would it be possible to add the IP address or hostname of the device that opened the door in the event logs?

nebhead, 2021-07-27:
> I have been using GarageZero for 2 weeks now and really love it. I have also changed the door status pic to these animated png files of Peter Griffin I like them :) I did have to modify the base.html, doorstatus.html and admin.html to make it look right. If your interested I will share the files.
> 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
> 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

LOL!  This is excellent, I love it!  Can you share a screen shot of the dashboard with the door open?  Truly terrific.

nebhead, 2021-07-27:
> Would it be possible to add the IP address or hostname of the device that opened the door in the event logs?

I haven't tried this before, but it's both a good idea and something that I can try to implement.  I'm slowly chipping away at a few other requests, so I'll give this a go.

nebhead, 2021-07-27:
FYI... I've also ordered a different type of magnetic switch (https://www.amazon.com/gp/product/B0154PTDFI) which I'm going to use to implement the door open state.  Hopefully that will get here before the end of the week and I can get started on this.

nebhead, 2021-07-27:
> > Would it be possible to add the IP address or hostname of the device that opened the door in the event logs?
>
> I haven't tried this before, but it's both a good idea and something that I can try to implement. I'm slowly chipping away at a few other requests, so I'll give this a go.

Appears it's pretty simple to grab the IP in flask using request, so implemented a quick & dirty WriteLog when then button is pressed in the WebUI which logs the IP from the client.

Also fixed a little bug where I was using the datetime module inconsistently.

Updates in the development branch here: https://github.com/nebhead/garage-zero/commit/7adb188af942e03fe1bc23edaa00cd31966b39d5

J0eK1ng, 2021-08-11:
Hi nebhead
I'm glad you like the animated png files. I'm glad you are adding the magnetic switch for the door open status and as a bonus it will display the close door animation much quicker as opposed to once the close door sensor is detected.

I'm back from vacation (totally offline) and will post screenshots shortly.

Cheers and keep up the good work.

Denis

J0eK1ng, 2021-08-11:
Ok here are the screenshots from my phone.
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

nebhead, 2021-08-11:
> Maybe just add the IP address to the Full Events Logs or else it will not fit on the cell phone main page. Its always nice to know what device opened the doot.

Yeah, I like that idea.  Maybe the short-log (on the dashboard) just displays a short message only for all of the different events.  I'll have to incorporate that.

My SD-Card failed on my garage-zero today :( so I might take this opportunity to completely overhaul some things.

nebhead, 2021-08-15:
BTW - IP logging doesn't seem to work with nginx doing reverse proxy.  :(  Works fine when I'm testing with flask only, but once there are a few more layers involved (i.e. nginx and gunicorn), it just shows the local IP.  Anyway, will require more work.

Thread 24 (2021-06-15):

Password in Browser before you can Open the Garage

ZyginRNS, 2021-06-15:
Hi i wanted to ask, if you Can protect the Garage door being  Opend With a password or anything like That, because i wanted to make a Little touchpad Outside the Garage, if my mobile phone is Empty Or anything like That

nebhead, 2021-06-16:
Oh, that's a very interesting idea.  I'm thinking maybe a separate keypad, touchscreen or something, maybe a companion application that can be installed on another device that is mounted outside.  What kind of touch pad were you thinking?  Would you be opposed to using an Arduino device?

I'm away from my workshop for a few more weeks, but this sounds like something I might want to implement myself.

ZyginRNS, 2021-06-16:
i thaught about an  pc like an little raspberry pi, with just a little screen and an pinpad where you can only acces the website to open the door

nebhead, 2021-06-19:
Right, so what I was thinking about was perhaps using an Arduino based system based on an ESP8266 platform so it can communicate over Wi-Fi with the garage door controller, and then run on batteries only when in use.  What we could implement is an API Key system that will allow devices to trigger the garage door button with a specific URL + API Key that can be securely generated.

So, maybe a D1-Mini (they are really cheap on Amazon) hooked up to a keypad matrix and a couple of LED's. Then have a switch that turns on the system, and waits for keypad input, for a specific PIN code, which triggers an API call.  This can all be hardcoded to the device firmware and would be reasonably secure.  Since the D1-Mini is very low power, we could probably run this from a few AA batteries, and if it's off until a switch is activated (i.e. like the keypad cover being lifted), then it won't consume any power just sitting there.

It might take a second for the system to boot, but it's better than a raspberry pi or something, which can take over a minute to boot.  Also, it's pretty secure because someone can't just steal it, or hack into it to get it to work.  They'd still have to guess your PIN code to trigger the door open command.  At least I don't think there is a way for someone to dump the firmware on these things.  But honestly, if they went to that much trouble, there are easier ways to get into a garage. :)

A keypad like this (https://www.amazon.com/dp/B000TA8PE4/) and D1 Mini (https://www.amazon.com/AITRIP-NodeMcu-Internet-Development-Compatible/dp/B08C7FYM5T) some LEDs, a tack switch and a 3D printed enclosure would make this look pretty slick.  Could even put a solar charger on this thing to keep rechargeable batteries topped off.  This is kind getting me excited. :)

J0eK1ng, 2021-07-04:
I'm all for security and all but if your going to implement a password protected website can you put it a yes/no variable in your code? This would allow us to decide if we want that feature or not.  I don't need or want to have to input a pwd every time i want to open/close my garage door.
Now I understand this is important for an external keypad but not for the main web site. Just a thought.

nebhead, 2021-07-11:
Yep, definitely could implement an option to leave this open for those who want to.  It will take me some time, but I will definitely work on this idea.  It looks like in Flask, the session can put a cookie on the device and thus would only need to log in once.

I've ordered some keypads from Amazon to start playing around with this.

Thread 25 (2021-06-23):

(Help!) Access outside local network

nintendowii111, 2021-06-23:
I would like to make this work over the web. How does one use the recommended PiVPN to do this?

Sorry I’m new to this  ;)

nebhead, 2021-06-23:
Since this is a web based application, a local VPN is currently needed so that you can access your instance of the garage door opener at it's IP address. With that said, there are number of ways to setup a VPN at home so that you can access your home network when you are away.  The easiest way is to use PiVPN on another raspberry Pi in your house (https://www.pivpn.io/).  It's very straight forward to setup on a freshly installed Raspberry Pi.  I'd highly recommend using WireGuard as it's very easy to setup on your phone, PC or tablet with the right app using a QR code.  Once you establish your VPN,  you should be able to go to the IP address of your garage door in your browser, just like you do normally and get access.

I've considered other ways to make the door accessible outside of the home network, but security is a huge concern.  And it may require a third party server to service an API or something.  If anyone out there knows how to do this properly, please do let me know. :)

nintendowii111, 2021-06-23:
> Since this is a web based application, a local VPN is currently needed so that you can access your instance of the garage door opener at it's IP address. With that said, there are number of ways to setup a VPN at home so that you can access your home network when you are away. The easiest way is to use PiVPN on another raspberry Pi in your house (https://www.pivpn.io/). It's very straight forward to setup on a freshly installed Raspberry Pi. I'd highly recommend using WireGuard as it's very easy to setup on your phone, PC or tablet with the right app using a QR code. Once you establish your VPN, you should be able to go to the IP address of your garage door in your browser, just like you do normally and get access.
>
> I've considered other ways to make the door accessible outside of the home network, but security is a huge concern. And it may require a third party server to service an API or something. If anyone out there knows how to do this properly, please do let me know. :)

I understand security is a concern, but I'd like to at least see it function outside the network without security. I don't have another raspberry pi (and don't want another one lol); could you tell me how could I go about using my router to allow the server on the pi to be broadcasted in the public?

nebhead, 2021-06-24:
So, if security is completely not a concern, then you would simply need to open a port on your router to forward to your raspberry pi.  Depending on your router manufacturer, you'll need to log into their interface, and assign a port forward.  Maybe select a random port like 8086 and then forward that to your Pi IP with port 80.  When you access your external IP from outside your house, the requests will be forwarded to the Pi inside your network.

If your internet provider changes your IP on you, you'll want to setup a dynamic DNS service as well. This might not be supported by your router, but many bigger manufacturers have something similar like No-IP, to allow you to assign a human readable domain name to your IP.

Anyway, with all of this said, anyone on the internet would have access to the webUI and possibly be able to hack into your Pi, and then use that as a basis for a hack on the rest of your computers in your network.  Anything is possible.  Ransomware, bitcoin mining, etc.  So do this at your own peril.

nintendowii111, 2021-06-24:
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

I was afraid that opening ports for the pi would expose everything else on the network, if it only would leave the pi wide open I would be ok with it, but I don't want to affect any other devices on the network.

Although, I've been looking into getting this project to work online and found [Ngrok](https://ngrok.com/).
Have you tried looking into this service as a means for outside access?

Thanks again!

nebhead, 2021-06-24:
I mean, technically speaking if you forward to port 80 on the Pi itself, that is the only device that the outside world will see.  So, if you do your diligence, and correctly secure the port 80 interface on the Pi, then you should be fine.  There are lots of applications that work this way and are designed with security in mind.  I'm just not confident that this garage door opener is secure and has all potential attack vectors handled. :)  And if someone were to find some crack in the security of the Pi (nginx, flask, etc.) then they could launch attacks on the rest of the network.  Anyway - let me take a look at Ngrok and see if it can be applied in this instance.  Having some kind of secure tunnel is always good for overall security.  I probably should build in some kind of secure API to allow for opening / closing the door from other applications (i.e. home assistant), which would probably address the problem in this case.

nintendowii111, 2021-07-01:
> I mean, technically speaking if you forward to port 80 on the Pi itself, that is the only device that the outside world will see. So, if you do your diligence, and correctly secure the port 80 interface on the Pi, then you should be fine. There are lots of applications that work this way and are designed with security in mind. I'm just not confident that this garage door opener is secure and has all potential attack vectors handled. :) And if someone were to find some crack in the security of the Pi (nginx, flask, etc.) then they could launch attacks on the rest of the network. Anyway - let me take a look at Ngrok and see if it can be applied in this instance. Having some kind of secure tunnel is always good for overall security. I probably should build in some kind of secure API to allow for opening / closing the door from other applications (i.e. home assistant), which would probably address the problem in this case.

Hey again, I'm curious if you wouldn't mind making a few new changes to Garagezero. I have it setup and working and definitely enjoy it. What I wouldn't mind having, however, is 12-hour time instead of 24, also, making the event log be from up-down, most recent, to least recent. i.e. most recent button press log at top of history. Thirdly, option to remove door-status for those who do not use reed switches to know status of the door. and lastly, change the big green door button to have visual feedback when pressed? i.e., make it to where it turns yellow when pressed, and doesnt allow to be pressed again for a few seconds and then turns back to green. This sequence would indicate that the button press was received by the server and would stop a double press if accidentally it was double pressed by the user.

Thanks again for the help!

nebhead, 2021-07-01:
Yeah I'm definitely up for making improvements and adding features.  I'm
away from my workshop for the next week and a half but I will take a look
at these when I return.  I'm actually thinking I will implement a password
feature as you asked about before because I think it might be useful in
your case and in case of having a secondary keypad.

On Thu, Jul 1, 2021, 11:15 AM nintendowii111 ***@***.***>
wrote:

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

nebhead, 2021-07-25:
FYI:  Just added sort capability in the development branch with the last commit.

https://github.com/nebhead/garage-zero/commit/73ee534b427767fd35dd6a4fc581d2b5e016fdf9

nintendowii111, 2021-07-26:
> FYI: Just added sort capability in the development branch with the last commit.
>
> [73ee534](https://github.com/nebhead/garage-zero/commit/73ee534b427767fd35dd6a4fc581d2b5e016fdf9)

Thanks!

nebhead, 2021-07-26:
FYI: Just added 12H/24H select button so that events will be displayed in the UI as selected.

https://github.com/nebhead/garage-zero/commit/3fea0cf7d125b7be8f5541cc460cddcdf39f4d48

nintendowii111, 2021-07-26:
> FYI: Just added 12H/24H select button so that events will be displayed in the UI as selected.
>
> [3fea0cf](https://github.com/nebhead/garage-zero/commit/3fea0cf7d125b7be8f5541cc460cddcdf39f4d48)

Hey, how does one install the update? Will redoing the install process overwrite the files and stuff?

nebhead, 2021-07-26:
You'll need to first update your git repo by doing a pull, then switch to the development branch and reboot.

Use SSH to log into your pi, then:
```
pi@garage-zero:~ $ cd garage-zero/
pi@garage-zero:~ $ sudo git pull
```
This should get the latest from GitHub, including the development branch.  If you see errors, it's possible that you may have modified the original files which means GitHub can't resolve the conflicts.  You can reset back to the original by running `sudo git reset --hard`, but keep in mind that your changes will be lost.

```
pi@garage-zero:~ $ sudo git checkout development
```
This should switch you to the development branch.

Then reboot the system.
```
pi@garage-zero:~ $ sudo reboot
```

Hopefully, this will work.  :)  Let me know how it goes.

nebhead, 2021-07-27:
Oops, found a bug.  Also implemented another minor feature.  Updates are here: https://github.com/nebhead/garage-zero/commit/7adb188af942e03fe1bc23edaa00cd31966b39d5

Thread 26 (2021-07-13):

Open / Close with voice using Google Home

silentfire619, 2021-07-13:
Is it possible to integrate this with Google Home to use voice command to open and close the door?

nebhead, 2021-07-13:
As it stands currently, I haven't yet implemented an API to do this, however it is definitely in the plan to implement this API in an upcoming version.  That said, there are some items to remember:

1. Google Home (or Alexa) integration requires a third party server that sits on the internet that can connect with your Google Assistant services, and send a SSL Webhook to the garage door on your network.  That means you'll need to use something like IFTTT, or HomeAssistant to be that intermediary.  Both of these are pay services to use outside of your network (although it's possible to get some of these for free).
2. **Security:**  Adding an API to the garage door may require you open a port to this device.  Exposing your IoT devices to the internet can be tricky business and may put your home network at risk.  I'll do my best to make this as secure as I can, but there are always risks.  My plan is to create this API for use with HomeAssistant, behind your firewall, to let HomeAssistant do all of the security for you.

No timeline yet, but i'm looking at tackling this in the next few weeks, along with another companion project for an outdoor keypad to open the door without your cell phone.

nebhead, 2021-07-13:
One other thing is that for home security, you might not want to have some be able to shout at your home assistant (inside your house) to open your garage door.  So might be good to have a passcode to open the door, but no such passcode to close it.

silentfire619, 2021-07-13:
Thank you for your quick reply. I have IFTTT and was trying to get it working with that but had no luck (I do not really know what I am doing there.) I have already allowed outside access to the PI by forwarding port XXXX to port 80. I appreciate all the work you have and continue to do. I will be looking for to this if / when you complete it.

nebhead, 2021-07-13:
Sure no problem.  I would highly recommend closing up that port for now.  After we get the updated feature implemented, we'll likely open up 443 (for HTTPS communication to the API only).  But for now, your Pi is exposed on port 80 and it can be exploited by a malicious actor.

silentfire619, 2021-07-13:
Wouldn't they need to know the port I am using to redirect to port 80 in order to really do anything?

nebhead, 2021-07-13:
So right now, if you have your Pi's port 80 opened to the internet, then someone could do remote discovery (port scan) and find your open port.  If it's GarageZero, then it would be the entire interface available on that port - and whatever else the Flask server is providing.  It might be possible for someone really smart to manipulate the commands on port 80 to do more malicious things.

In the future, we'll open up port 443 via the nginx reverse proxy to _just_ the API.  And to use the API, a unique API key will need to be passed through, encrypted with SSL.  All other traffic on that port will be ignored.  We can provide the API key to the webhook on IFTTT which can send commands that way.  The attack surface is much more limited, even if they discover your external port.

mdbrewer, 2022-08-03:
I would love to have the API feature added to this version. Do you take kickbacks/donations to enable?

nebhead, 2022-08-03:
> I would love to have the API feature added to this version. Do you take kickbacks/donations to enable?

Do you mean similar to the API that is implemented in v2 for Home Assistant (or other apps)?  I think it could be done pretty easily.  I could take a crack at it.

nebhead, 2022-08-04:
> Exactly that, thank you. I tried to install V2 with the HW setup from this build with no success. Thank you for putting this out there. Do you have a patreon to contribute?

Cool, yeah, I think I can make the changes with v1.  I was just looking at the v2 code to see if we could make the v1 hardware work properly - but I realized that there is a breaking change with the v2 implementation, to make it work with the old hardware configuration.  The relay gate is not implemented in the v2 (because it's not needed for the new hardware) and thus, is wouldn't work with the old hardware configuration.

However, you could operate without the relay gate at all (just like the v2 hardware).  This means a minor change to your relay wiring.  Basically have one end of the button wire into the common side of relay2 and the other to the NO (normally open) side of relay2.  And of course, remove the jumper wire that you have between relay1 & relay2.  This would only use one relay, which would be controlled by the raspberry Pi for simulating the button press.

If you make the above hardware change to the v1 setup, you can configure the v2 software settings in the webui as follows:

1.  Edit door settings (settings -> door settings -> edit default door:

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

2.  Remove the second sensor which isn't part of the original design

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

3.  Change the GPIO's to match the original design

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

relay_pin = 15	 # GPIO 15, Pin 10 (RasPi Header)  -> Goes to relay IN2 (Relay2)
switch_pin = 18 # GPIO 18, Pin 12 (RasPi Header) -> Goes to magnetic switch

And that should be all you really need to do.

One item of note, is that GPIO 14 & 15 may toggle on boot because they are used for console output/input.  This behavior can be disabled in raspi-config.
```
Interfacing Options -> Serial -> Would you like a login shell to be accessible over serial? No
```
If that doesn't appeal to you, I can still make the changes to the Garage Zero v1 code, but will probably be at least this weekend before I get a chance to work on it.

Thanks!

mdbrewer, 2022-08-05:
I actually tried V2 with the exact hardware setup you suggested earlier. I ran into the door being triggered on device reboot, as well as notifications not being saved. I reverted back to keep the house secure.
Thank you for maintaining this!

nebhead, 2022-08-06:
> I actually tried V2 with the exact hardware setup you suggested earlier. I ran into the door being triggered on device reboot, as well as notifications not being saved. I reverted back to keep the house secure. Thank you for maintaining this!

Got it.  I think the issue with the door triggering on reboot is due to GPIO 14 & 15.  If you move to another GPIO, this shouldn't happen anymore.  Or you could disable the serial interface on those pins and that should also help.  As for the notifications, not exactly sure what's going on there.  Regardless, let me look into updating the original garage zero this weekend and hopefully it's not too bad.  Might need your help to test it out and make sure it's good to go.

nebhead, 2022-08-06:
Working on this in the development branch... should push soon, but will definitely need you to test because I don't have this setup with real hardware.

nebhead, 2022-08-06:
> I actually tried V2 with the exact hardware setup you suggested earlier. I ran into the door being triggered on device reboot, as well as notifications not being saved. I reverted back to keep the house secure. Thank you for maintaining this!

OK, that wasn't too bad.  Added this to the development branch for you to check out.  Link to the commit is here: https://github.com/nebhead/garage-zero/commit/1dcaea258ca960153775f9b92dd0a7737ed50e46

First, you'll need to pull down the development branch on your instance.  SSH into your Pi, then navigate to the garage zero folder:

```bash
$ cd ~/garage-zero
```
Next, stop all of the currently running garage-zero services:

```
$ supervisorctl stop all
```

Then you will want to fetch the latest from github and change the branch to development:

```bash
$ git pull
$ git checkout development
```
Assuming that goes well, you'll need to backup your settings.json file, or delete it.  Unfortunately, there are some updates that require it to be regenerated.  This means you will need reset your settings in the UI.

```bash
$ sudo mv settings.json settings.backup
```

Then, reboot and test!

```bash
$ sudo reboot
```

Once you have rebooted, go to your browser and bring up the garage-zero WebUI.  Go to the admin/settings screen and enable the API.  Then in the API card, click the link to show the example Home Assistant YAML file.  Copy this information (confirm the IP address is correct) into your Home Assistant YAML file.  Check the configuration in Home Assistant and make sure you restart Home Assistant (this is important, because otherwise it may not proper install the cover components).  You should then be able to go to your dashboard and add the Garage Door entity.

Please test and let me know how it goes.  If it's all good, I will move this to the main branch for all to benefit from.

If the mood strikes you, you can feel free to gift me what you think is fair here: https://paypal.me/benparmeter

Good luck!

mdbrewer, 2022-08-08:
Works flawlessly! Thank you for integrating the capability.

nebhead, 2022-08-08:
Outstanding!  You are very welcome and thanks for contributing to the wine fund.  I'll go ahead and merge this into the main branch.
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
nebhead, 2023-02-11:
Hate to be a bother, but could you put that code between the code tags?  Example:

\`\`\`yaml

Your code goes here.

\`\`\`

YAML has very particular formatting with indentations, so it make a difference looking at the proper formatting.

silentfire619, 2023-02-11:
Not a bother at all. I have edited the original post with the code. I appreciate all your help!

nebhead, 2023-02-11:
Honestly, this YAML looks perfectly fine to me.  I would restart the Home Assistant server, perhaps manually, to reload all of the elements (i.e. cover integrations).  This can sometimes be the culprit when things are misbehaving.

silentfire619, 2023-02-11:
Ok thank you for you help. I will mess around with this more tomorrow.

nebhead, 2023-02-11:
> Ok thank you for you help. I will mess around with this more tomorrow.

Sounds good.  Good luck and let me know if you discover anything.  Home Assistant can sometimes be infuriating, until it works.

silentfire619, 2023-02-11:
So I have removed all the code, unlinked Home Assistant from Google Assistant, updated Home Assistant, added the code back in with your change, and linked Home Assistant. I have only added the cover to Google and now the door opens and closes but I am back at the original problem where the door will open if it is told to close while being closed already.

nebhead, 2023-02-11:
> So I have removed all the code, unlinked Home Assistant from Google Assistant, updated Home Assistant, added the code back in with your change, and linked Home Assistant. I have only added the cover to Google and now the door opens and closes but I am back at the original problem where the door will open if it is told to close while being closed already.

Hmm... and we are sure it's only the cover that is exposed to Google Assistant?  Same code as above?  It shouldn't execute the command switch.turn_off if the sensor is open.  Maybe check your developer tools, to make sure that the sensor is reporting closed when the door is closed.

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

silentfire619, 2023-02-11:
I was mistaken it is working now. When I was testing it I told Google to close the garage door as pretty much as soon as it closed.

nebhead, 2023-02-11:
> I was mistaken it is working now. When I was testing it I told Google to close the garage door as pretty much as soon as it closed.

Woohoo!  Success.  Thanks for pointing this out.  Huge security concern.  BTW... I have updated the repo with the new YAML template.  I've also applied the same fix to the pause function.

silentfire619, 2023-02-11:
You are welcome and thank you for the help and everything you do.

nebhead, 2023-02-11:
> You are welcome and thank you for the help and everything you do.

You are welcome!  Happy to help.

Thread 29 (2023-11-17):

Door Status only showing "green open"

AppleManDos, 2023-11-17:
Hi. Thank you for the great work and explanations.

I powered it up for the first time yesterday and the Door Status shows "green closed" regardless of whether the magnetic switch is connected or in proximity with its contact. I was using a long length of Cat5 wires to reach the door.

I tested my magnetic switch using a multi-meter and it works.

I powered it off and left it overnight.

Today, I hooked it up again to troubleshoot the magnetic switch.

I noticed the Door Status was working "red open" / "green closed" with the magnetic switch connected with a very short wire. When I reconnected the long wire, the status remains as "green closed" like it did yesterday. I cannot get it to show the "red open" state again. I have disconnected the magnetic switch, used short wires again, swapped polarity, restarted everything. Still showing "green closed" no matter what I do.

I have tried different power supplies (0.7 A to 2.3 A) also.

I would expect a disconnected magnetic switch to show "red open" but it only showed up once. What could be causing it to constantly show "green closed"?

I am using both the 1 kΩ and 10 kΩ resistors. Should I eliminate them and change to GPIO 2 or 3 and change control.py as mentioned in the note (Optional Design Change)?

nebhead, 2023-11-17:
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

> I am using both the 1 kΩ and 10 kΩ resistors. Should I eliminate them and change to GPIO 2 or 3 and change control.py as mentioned in the note (Optional Design Change)?

Hmm... this should all work just fine with the resistor setup that is documented, so further testing is needed.  If you have a multi-meter, can you check the voltage level at GPIO18 (Pin 12), while powered on and the magnetic switch is OPEN and when the magnetic switch is CLOSED.

Also, just to make sure, are you using the same magnetic switch that is linked in the documentation?   (https://www.amazon.com/dp/B0009SUF08/ref=cm_sw_em_r_mt_dp_U_htppCbJ7B52KG)

AppleManDos, 2023-11-17:
I took the resistors out and it worked but not for long. I think my daughterboard was giving me trouble so I removed it completely. Things are working properly now. I will test it for a while and report back.

I think the resistors were fine. It was probably just my wiring.

nebhead, 2023-11-17:
Great to hear!  Hope it goes smoothly from here on out.  Enjoy!

AppleManDos, 2024-01-04:
It has been running very well for several weeks now. I installed an infrared camera. The magnetic switch I used is a cheap one from [Aliexpress](https://www.aliexpress.com/item/1005003498078487.html).

For remote access, I am using Zerotier.

Everything working great.

nebhead, 2024-01-04:
> Everything working great.

Awesome!  Glad it's working well for you, and thank you for checking back in and giving an update!  Enjoy and happy new year!

Closed 2024-01-04.

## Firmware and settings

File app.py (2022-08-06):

from flask import Flask, request, render_template, make_response, redirect, abort, jsonify
import time
import datetime
import os
import secrets
from common import *

app = Flask(__name__)
settings = ReadSettings()

@app.route('/', methods=['POST','GET'])
def index():
	global settings
	if (request.method == 'POST'):
		response = request.form
		if('listorder' in response):
			if(response['listorder'] == 'topdown'):
				settings['misc']['listorder'] = 'topdown'
			else:
				settings['misc']['listorder'] = 'bottomup'
			WriteSettings(settings)
		if('24htime' in response): 
			if(response['24htime'] == 'true'):
				settings['misc']['24htime'] = True
			else:
				settings['misc']['24htime'] = False 
			WriteSettings(settings)

	return render_template('index.html', pagetheme=settings['misc']['theme'], settings=settings)

@app.route('/status')
def doorstatus():
	states = ReadStates()
	return render_template('doorstatus.html', state=states['inputs']['switch'])

@app.route('/shortlog')
def shortlog():
	global settings
	door_history, events = ReadLog(10, twentyfourhtime=settings['misc']['24htime'])
	return render_template('shortlog.html', door_history=door_history, events=events, settings=settings)

@app.route('/button')
def button():
	states = ReadStates()
	states['outputs']['button'] = True  		# Button pressed - Set state to 'on'
	WriteStates(states)		# Write button press to file
	ipaddress = request.remote_addr
	event = 'Button Press from WebUI [' + ipaddress + ']'
	WriteLog(event)
	return redirect('/')

@app.route('/history', methods=['POST','GET'])
def history():
	global settings

	if (request.method == 'POST'):
		response = request.form

		if('listorder' in response):
			if(response['listorder'] == 'topdown'):
				settings['misc']['listorder'] = 'topdown'
			else:
				settings['misc']['listorder'] = 'bottomup'
			WriteSettings(settings)
		if('24htime' in response): 
			if(response['24htime'] == 'true'):
				settings['misc']['24htime'] = True
			else:
				settings['misc']['24htime'] = False 
			WriteSettings(settings)

	door_history, events = ReadLog(twentyfourhtime=settings['misc']['24htime'])

	return render_template('history.html', door_history=door_history, events=events, pagetheme=settings['misc']['theme'], settings=settings)

@app.route('/admin/<action>', methods=['POST','GET'])
@app.route('/admin', methods=['POST','GET'])
def admin(action=None):
	states = ReadStates()
	global settings 
	settings = ReadSettings()

	if action == 'reboot':
		event = "Reboot Requested."
		WriteLog(event)
		os.system("sleep 3 && sudo reboot &")

		#Show Reboot Splash
		return render_template('shutdown.html', action=action, pagetheme=settings['misc']['theme'])

	if action == 'shutdown':
		event = "Shutdown Requested."
		WriteLog(event)
		os.system("sleep 3 && sudo shutdown -h now &")

		#Show Shutdown Splash
		return render_template('shutdown.html', action=action, pagetheme=settings['misc']['theme'])

	if (request.method == 'POST') and (action == 'settings'):
		response = request.form

		if('from_email' in response):
			if(response['from_email']!=''):
				print("from_email: " + response['from_email'])
				settings['email']['FromEmail'] = response['from_email']

		if('to_email' in response):
			if(response['to_email']!=''):
				print("to_email: " + response['to_email'])
				settings['email']['ToEmail'] = response['to_email']

		if('server' in response):
			if(response['server']!=''):
				print("Server: " + response['server'])
				settings['email']['SMTPServer'] = response['server']

		if('port' in response):
			if(response['port']!=''):
				print("Port: " + response['port'])
				settings['email']['SMTPPort'] = int(response['port'])

		if('username' in response):
			if(response['username']!=''):
				print("username: " + response['username'])
				settings['email']['Username'] = response['username']

		if('password' in response):
			if(response['password']!=''):
				print("password: " + response['password'])
				settings['email']['Password'] = response['password']

		use_tls = 'use_tls' in response
		if(use_tls!=settings['email']['UseTLS']):
			print("useTLS: %s" % use_tls)
			settings['email']['UseTLS'] = use_tls

		if('public_url' in response):
			if(response['public_url']!=''):
				print("public_url: " + response['public_url'])
				settings['misc']['PublicURL'] = response['public_url']

		if('timeout' in response):
			if(response['timeout']!=''):
				print("Timeout: " + response['timeout'])
				settings['notification']['minutes'] = int(response['timeout'])

		if('reminder' in response):
			if(response['reminder']!=''):
				print("Reminder: " + response['reminder'])
				settings['notification']['reminder'] = int(response['reminder'])

		if('iftttapi' in response):
			if(response['iftttapi']!=''):
				print("IFTTT API Key: " + response['iftttapi'])
				settings['ifttt']['APIKey'] = response['iftttapi']

		settings['notification']['notify_on_open'] = "off"  # Turn off notify_on_open if no response from POST

		if('notify_on_open' in response):
			if(response['notify_on_open']!=''):
				print("Notify on Open: " + response['notify_on_open'])
				settings['notification']['notify_on_open'] = response['notify_on_open']

		if('pushover_apikey' in response):
			if(response['pushover_apikey']!=settings['pushover']['APIKey']):
				print("Pushover API key: " + response['pushover_apikey'])
				settings['pushover']['APIKey'] = response['pushover_apikey']

		if('pushover_userkeys' in response):
			if(response['pushover_userkeys']!=settings['pushover']['UserKeys']):
				print("Pushover User keys: " + response['pushover_userkeys'])
				settings['pushover']['UserKeys'] = response['pushover_userkeys']

		if('theme' in response):
			print(response['theme'])
			settings['misc']['theme'] = response['theme']

		if('enable_api' in response):
			print(response['enable_api'])
			if response['enable_api'] == 'true':
				settings['api_config']['enable'] = True
				if settings['api_config']['apikey'] == '':
					settings['api_config']['apikey'] = gen_api_key(32)
			else:
				settings['api_config']['enable'] = False

		if('gen_api' in response):
			print(response['gen_api'])
			if response['gen_api'] == 'true':
				settings['api_config']['apikey'] = gen_api_key(32)

		WriteSettings(settings)
		event = "Settings Updated."
		WriteLog(event)

	uptime = os.popen('uptime').readline()

	cpuinfo = os.popen('cat /proc/cpuinfo').readlines()

	return render_template('admin.html', action=action, uptime=uptime, cpuinfo=cpuinfo, settings=settings, pagetheme=settings['misc']['theme'])

@app.route('/manifest')
def manifest():
    res = make_response(render_template('manifest.json'), 200)
    res.headers["Content-Type"] = "text/cache-manifest"
    return res

@app.route('/api/<action>', methods=['POST','GET'])
def api(action=None):
	global settings 

	apikey = settings['api_config']['apikey']
	doorname = settings['misc']['doorname']

	if (settings['api_config']['enable'] == True) and (apikey == action):
		if (request.method == 'POST'):
			if not request.json:
				event = 'Local API Call Failed - Local API interface not enabled.'
				WriteLog(event)
				abort(400)
			else:
				if('DoorButton' in request.json):
					states = ReadStates()
					states['outputs']['button'] = True  		# Button pressed - Set state to 'on'
					WriteStates(states)		# Write button press to file
					event = f'Local API Call Success. Door button [{doorname}] pressed.'
					WriteLog(event)
					return jsonify({'result': 'success'}), 201
			return jsonify({'result': 'failed'}), 201

		if (request.method == 'GET'):
			door_output = {}
			door_output = {
				doorname: {
					'id': settings['misc']['id'],
					'status': {
						'limitsensorclosed': ''
					}
				}
			}

			states = ReadStates()
			state=states['inputs']['switch']
			
			door_output[doorname]['status']['limitsensorclosed'] = 'open' if state == 1 else 'closed'
		
			event = 'Local API Call Success. [GET]'
			WriteLog(event)
			return jsonify(door_output), 201

	event = 'Local API Call Failed.'	
	WriteLog(event)

	abort(404)

@app.route('/haexample')
def haexample():
	global settings 

	doorname = "Garage Door"

	server_ip = request.environ['HTTP_HOST']
	#print(request.environ)

	site_url_api = f"http://{server_ip}/api/{settings['api_config']['apikey']}"
	value_template = "{{ value_json['" + doorname + "']['status']['limitsensorclosed'] }}"
	
	resp = make_response(render_template('ha_example.yaml', site_url_api=site_url_api, value_template=value_template, doorname=doorname))
	resp.mimetype = 'text/plain'
	return resp

"""
Supporting Functions
"""

# Attribution to Vladimir Ignatyev on Stack Overflow
# https://stackoverflow.com/questions/41969093/how-to-generate-passwords-in-python-2-and-python-3-securely
def gen_api_key(length, charset="ABCDEFGHIJKLMNOPQRSTUVWXYZabcdefghijklmnopqrstuvwxyz0123456789"):
    return "".join([secrets.choice(charset) for _ in range(0, length)])


if __name__ == '__main__':
    app.run(host='0.0.0.0', debug=True) # use ,debug=True for debug mode

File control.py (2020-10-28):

#!/usr/bin/env python3
# *****************************************
# Garage Door Control Python script
# *****************************************
#
# Description: This script will read the states.txt file and set relays/LEDs
# upon any changes to that file.  This script also accepts input from the IR
# sensor and will write the states.txt file and set the relays appropriately.
#
# This script runs as a separate process from the Flask / Gunicorn
# implementation which handles the web interface.
#
# *****************************************

# Imports
import time
import datetime
import os
import json
import smtplib
import requests
from email.mime.multipart import MIMEMultipart
from email.mime.text import MIMEText
import urllib.request, urllib.parse, urllib.error

import RPi.GPIO as GPIO
from common import *

# GPIO Definitions
relay_pin = 15			# GPIO 15, Pin 10 (RasPi Header)
relay_gate_pin = 14		# GPIO 14, Pin 08 (RasPi Header)
switch_pin = 18			# GPIO 18, Pin 12 (RasPi Header)

# Init GPIO's to default values / behavior
GPIO.setmode(GPIO.BCM)

GPIO.setup(relay_pin, GPIO.OUT, initial=0) # Setup Relay IN1 on GPIO
GPIO.setup(relay_gate_pin, GPIO.OUT, initial=0) # Setup Relay IN2 on GPIO

GPIO.setup(switch_pin, GPIO.IN, pull_up_down=GPIO.PUD_DOWN) # Setup Magnetic Switch on GPIO18 (set pull down)

timer_start = 0 # Initialize timer_start variable, set to 0
reminder_timer_start = 0 # Initialize reminder_timer_start, set to 0
notify_on_close = False # Initialize the flag for notifying that the door has closed
opened_at = 0 # Time the door was opened

def SendEmail(settings, notifyevent):
	# WriteLog("[DEBUG]: SndEmail Function. " + notifyevent)
	now = datetime.datetime.now().strftime('%Y-%m-%d %H:%M')

	if notifyevent == "GarageEvent_Open_Alarm" or notifyevent == "GarageEvent_StillOpen_Alarm":
		open_minutes = int((time.time() - opened_at) / 60)
		notifymessage = "GarageZero wants you to know that your garage door has been open for %d minutes at %s" % (open_minutes, now)
		subjectmessage = "GarageZero: Door Open for %d Minutes" % open_minutes
	elif notifyevent == "GarageEvent_Closed":
		notifymessage = "GarageZero wants you to know that your garage door was closed at " + now
		subjectmessage = "GarageZero: Closed at " + str(now)
	elif notifyevent == "GarageEvent_Notify_on_Open":
		return # don't send emails for these
	else:
		notifymessage = "Whoops! GarageZero had the following unhandled notify event: " + notifyevent + " at " + now
		subjectmessage = "GarageZero: Unknown Notification at " + str(now)

	notifymessage += "\n\nCheck: " + settings['misc']['PublicURL']

	try:
		fromaddr = settings['email']['FromEmail']
		toaddr = settings['email']['ToEmail']
		toaddrlist = [addr.strip() for addr in toaddr.split(',')] # split on commas and strip out any spaces

		msg = MIMEMultipart()
		msg['From'] = fromaddr
		msg['To'] = ', '.join(toaddrlist)
		msg['Subject'] = subjectmessage
		body = notifymessage
		msg.attach(MIMEText(body, 'plain'))

		server = smtplib.SMTP(settings['email']['SMTPServer'], settings['email']['SMTPPort'])
		if settings['email']['UseTLS']:
			server.starttls()
		if settings['email']['Username']:
			server.login(settings['email']['Username'], settings['email']['Password'])
		text = msg.as_string()
		server.sendmail(fromaddr, toaddrlist, text)
		server.quit()

		for addr in toaddrlist:
			event = subjectmessage + ". E-mail notification sent to: " + addr
			WriteLog(event)

	except smtplib.SMTPException as e:
		event = "E-mail notification failed. SMTPLib general exception: %s" % e
		WriteLog(event)
	except Exception as e:
		event = "E-mail notification failed, with exception: %s" % e
		WriteLog(event)
	return()


def SendPushoverNotification(settings,notifyevent):
	now = datetime.datetime.now().strftime('%Y-%m-%d %H:%M')

	if notifyevent == "GarageEvent_Open_Alarm" or notifyevent == "GarageEvent_StillOpen_Alarm":
		open_minutes = int((time.time() - opened_at) / 60)
		notifymessage = "GarageZero wants you to know that your garage door has been open for %d minutes at %s" % (open_minutes, now)
		subjectmessage = "GarageZero: Door Open for %d Minutes" % open_minutes
	elif notifyevent == "GarageEvent_Closed":
		notifymessage = "GarageZero wants you to know that your garage door was closed at " + now
		subjectmessage = "GarageZero: Closed at " + str(now)
	elif notifyevent == "GarageEvent_Notify_on_Open":
		notifymessage = "GarageZero wants you to know that your garage door was just opened at " + now
		subjectmessage = "GarageZero: Opened at " + str(now)
	else:
		notifymessage = "Whoops! GarageZero had the following unhandled notify event: " + notifyevent + " at " + now
		subjectmessage = "GarageZero: Unknown Notification at " + str(now)
	
	url = 'https://api.pushover.net/1/messages.json'
	for user in settings['pushover']['UserKeys'].split(','):
		try:
			r = requests.post(url, data={
				"token": settings['pushover']['APIKey'],
				"user": user.strip(),
				"message": notifymessage,
				"title": subjectmessage,
				"url": settings['misc']['PublicURL']
			})
			WriteLog('Pushover Response: ' + r.text)
			WriteLog(subjectmessage + ". Pushover notification sent to: " + user.strip())

		except Exception as e:
			WriteLog("Pushover Notification to %s failed: %s" % (user, e))
		except:
			WriteLog("Pushover Notification to %s failed for unknown reason." % (user))


def SendIFTTTNotification(settings,notifyevent):
	# WriteLog("[DEBUG]: SendIFTTTNotification Function. " + notifyevent)

	key = settings['ifttt']['APIKey']
	url = 'https://maker.ifttt.com/trigger/' + notifyevent + '/with/key/' + key

	if notifyevent == "GarageEvent_Open_Alarm":
		query_args = { "value1" : str(settings['notification']['minutes']) }
	elif notifyevent == "GarageEvent_StillOpen_Alarm":
		open_minutes = int((time.time() - opened_at) / 60)
		query_args = { "value1" : open_minutes }
	else:
		query_args = {}

	try:
		r = requests.post(url, data=query_args)
		WriteLog("IFTTT Notification Success: " + r.text)
	except:
		WriteLog("IFTTT Notification Failed: " + r.text)


def SendNotification(settings,notifyevent):
	if settings['email']['FromEmail'] != "":
		SendEmail(settings, notifyevent)
	if settings['pushover']['APIKey']:
		SendPushoverNotification(settings, notifyevent)
	if settings['ifttt']['APIKey'] != "0":
		SendIFTTTNotification(settings, notifyevent)


def ToggleRelay():
	# *****************************************
	# Function to Toggle Relay (and open/close the garage door)
	# *****************************************
	# Insert code to push button here
	GPIO.output(relay_pin, 1) 	#Turn on Relay
	time.sleep(0.5)			#Wait for 0.5s
	GPIO.output(relay_pin, 0)	#Turn off Relay
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

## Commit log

2019-01-19 It begins...
    The First Release!
    [Garage Zero Case.stl, Garage Zero Lid.stl]
2019-01-31 Now with supervisord
    Moved to supervisord (python supervisor library) instead of loading everything through cron at boot. This allows us to monitor the scripts, and in case any of them fail/error out they will be restarted automatically. Also, logs are generated for the running applications which is pretty handy for debug. Instructions on the new setup in the README.MD. If you're moving from the initial version, you'll want to remove the @reboot line from your crontab by running sudo crontab -e and deleting that line. Enjoy!
2019-04-06 Bug fix for Send E-mail Function
    Fixed bug where one e-mail address was used, would fail.
    [control.py]
2019-04-06 show reasons for mail failure
    [control.py]
2019-04-08 fix Pushover settings being lost on changes to other fields
    [app.py]
2019-04-09 move state, settings and log routines to a common module to avoid duplication
    [app.py, common.py, control.py]
2019-04-10 handle case of reminders being turned off while the door is open
2019-04-11 Bug Fix: Swapped Button / Gate Pins
    Per the diagram in the readme, I had the pins swapped in the code. Fixing to ensure that we have consistency.
    [control.py]
2019-10-13 Update control.py
    Change Python2 to Python3 commands
    Fix tab/space mix for global
    [control.py]
2020-05-04 Detects OEM garage opener light, video added to app screen
    Photodiode detects OEM opener light on/off and switches the relay controlling the 12v LED strip. Video added to index.html. Additional readme doc for setup.
2020-05-04 Wiring diagram showing LED strip wiring
2020-10-28 Major Front End UI Overhaul / Fully Tested w/Python 3.x
    Lots of improvements for this version:
    * First and foremost, this is a full front-end upgrade using Bootstrap 4 to modernize the look
    * Updated the dashboard page to dynamically update/refresh the door status AND the short log of events in near real time - performance should generally be better
    * Added themes (via Bootstrap CSS files) which are select-able in the settings/admin page
    * Updated to move everything to Python 3.x including changes to the control.py script and to the auto-install script
    * Moved user submitted content to 'addons' folder, to be used for future optional addons that are not part of the base install
    * Squashed a f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
    [app.py, common.py, control.py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]
2021-07-25 Added Event Sort Capability
    Event sorting button added to dashboard and to history page. Sort selection is sticky and is stored in the settings json file for global usage.
2021-07-26 Option to select 12h or 24h time display
    Added a button to both the dashboard and history pages to display the time in 12h format or 24 hour format.
    Additional changes:
    * Changed button color for sort order buttons
    * Removed placeholder data for short log / history pages when less than 10 events in the log file. Now, only the events listed are displayed. And if no events, then no data is shown.
    [app.py, common.py]
2021-07-27 Quick IP logging for button presses
    Added IP when button is pressed from the WebUI.
    Also fixed a bug with the previous version where datetime module is called differently for reading log and for writing log.
    [app.py, common.py]
2023-02-10 Patch Potential Security Issue with HA and Google Assistant
    This change provides an update to the example template for the Home Assistant YAML configuration. It includes a change to prevent the door switch from being toggled if the door is already closed.
